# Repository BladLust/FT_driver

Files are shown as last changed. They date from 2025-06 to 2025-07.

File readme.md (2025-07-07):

## 硬件准备及安装

由于使用的FT电机与Leap Hand原装XC330电机尺寸、转轴、固定孔位置**完全相同**，仅有控制线插口位置不同，我们可以大致使用教程https://v1.leaphand.com/assembly

进行灵巧手硬件的安装。但正由于其控制线插口位置不同，我们需要对部分XC330配套的结构件进行调整并以3D打印的方式制作，我们需要替换其中由Dynamixel提供的电机支撑件。具体地，将所需的11个H101，10个S101以及6个S102使用本项目中`STLSubstitute`文件夹中对应的模型替换（由于它们足够相似，仿真中可以不用替换）。其中S101有两个版本，分别是需要8片的普通版和2片的Slim版。Slim版用于侧面不能突出的大拇指第二关节部分。

#### 3D打印部分

从LeapHand官网下载对应的模型进行打印，与本项目中提供的结构件一起即可组成灵巧手的全部硬件结构。官网下载部分的模型对于精度及强度要求均略低于直接用于固定电机的结构件，经过我们测试全部使用PLA进行打印即可满足基本强度要求，但使用更加坚固的PETG进行打印有助于减少需要由于误操作部件损坏重新组装灵巧手的次数。

#### 硅胶指尖制作

我们的演示程序使用的并非原版的Leap Hand灵巧手指尖。这些特制的指尖由硅胶倒模方式制作，经测试5度硅胶效果最好。在`CustomTip`文件夹中有制作硅胶部分用的内外模具的模型（取决于计划一次做好或分四次完成，打印4份或1份）及为指尖提供结构强度的”指骨“模型（安装在每个手指上，需要4个）。具体制作过程如下

- 打印内外模具（内模需要打印支撑以免打印失败）
- 在将与硅胶接触的部分涂抹一薄层凡士林以便之后脱模
- 在外模内倒入硅胶，以插入内模后刚好液面可接触到内模顶盖处为佳
- 放置与冰箱冷藏室中减速凝固，以便气泡排出。
- 在执行下一步之前先按照Leap Hand官方教程为指骨埋入土字铜花母
- 待其凝固后（具体多久并未测试，但放一晚肯定够了）脱模，并使用束带将其固定在指骨上。

#### 电机初始设置

12V DC电源上电，使用本项目中附带，由飞特提供的上位机软件`FD.exe` 进行各电机ID设置与波特率设置。（除非你懂得如何修改相关文件，不然推荐使用我们的电机ID顺序，如下图，波特率同理）。除大拇指外的三只手指从手掌到指尖按结构顺序ID分别为[x+1, x, x+2, x+3]，手指顺序为食指、中指、四指、拇指。对全新电机进行设置的具体顺序如下：

- 连接**单一一个电机**打开上位机软件，左上方波特率选择1000000，打开接口并电机搜索。
- 理论上新电机会以ID=1的状态被搜到，点击左侧搜到的电机，选择中上方的Programming页面。这里是各个寄存器的值，你可以通过这个界面具体检查电机各项设置
- 将ID改为你所需要的ID（我们建议先将16个电机依次更改ID为0-15并贴条记录，之后安装时按照对应ID安装）。**如果你不知道你在做什么，请保持副ID（Secondary ID)与主ID相同**
- 更改后电机会成为断连状态，重新给电机上电后重新搜索，电机将以新的ID出现。回到Programming界面将波特率baudrate改为115200。
- 换一个电机，重复以上步骤直至全部16个电机完成初始ID设置。

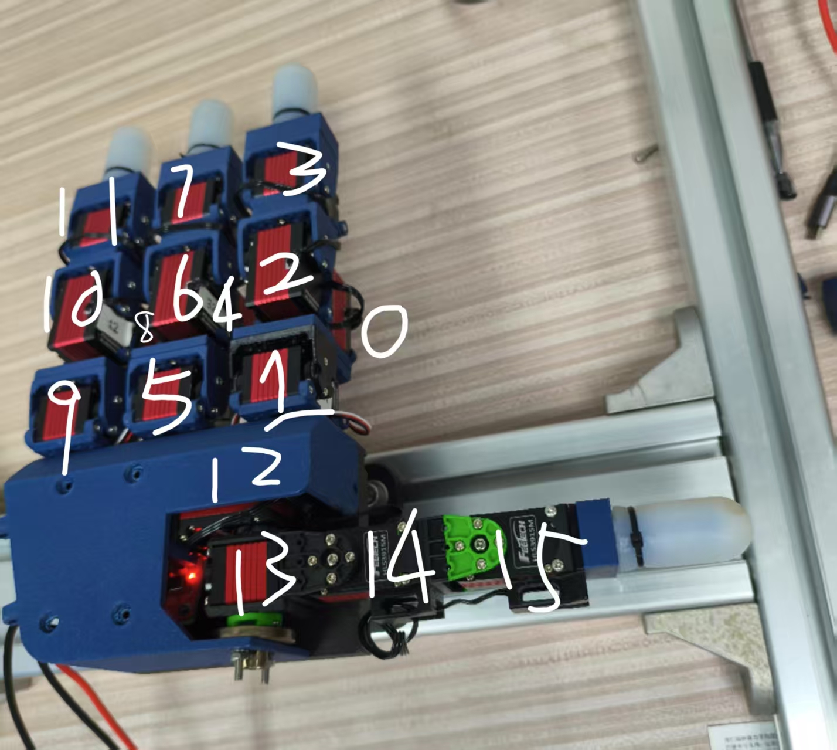
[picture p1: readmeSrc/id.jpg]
id


#### 组装

基本组装流程和LeapHand完全相同，但有几点需要注意

- 由于我们更改了S101及H101的模型，现在H101不同于原版，由于其单侧开槽的原因具有方向性。这一特点是为了能让螺丝固定部分更宽的修改版S101不影响手指活动空间的设计。你可以通过在一个单独电机上同时安装S101和H101了解其结构关系。在组装时应注意H101的开槽要面向S101一侧，具体地，对于2、3、4指来说其每指三个H101开槽的方向以手掌到指尖的顺序依次为掌心、手背、掌心。
- 电机有安装方向之分，但不管装正装反都不影响灵巧手本质结构，可以用电机Logo及型号两面的朝向分辨其安装方向。我们组装的灵巧手各电机方向如下图（2、3、4指朝向相同），如果你组装的手和我们的电机朝向相同，那么在完成后续“电机设置”一节完成后你应该得到正方向与Leap Hand官方仿真完全相同的结果。你可以选择使用与我们相反的方向安装0,3,4,7,8,11,12,13号电机，即可在后续“电机设置”一节中跳过使用mode3将电机反向的步骤。
- 组装过程中请时刻注意舵机间3pin接线的正反，若接反有烧毁舵机的风险！！！

| 拇指 | 其余三指 |
| :---: | :---: |
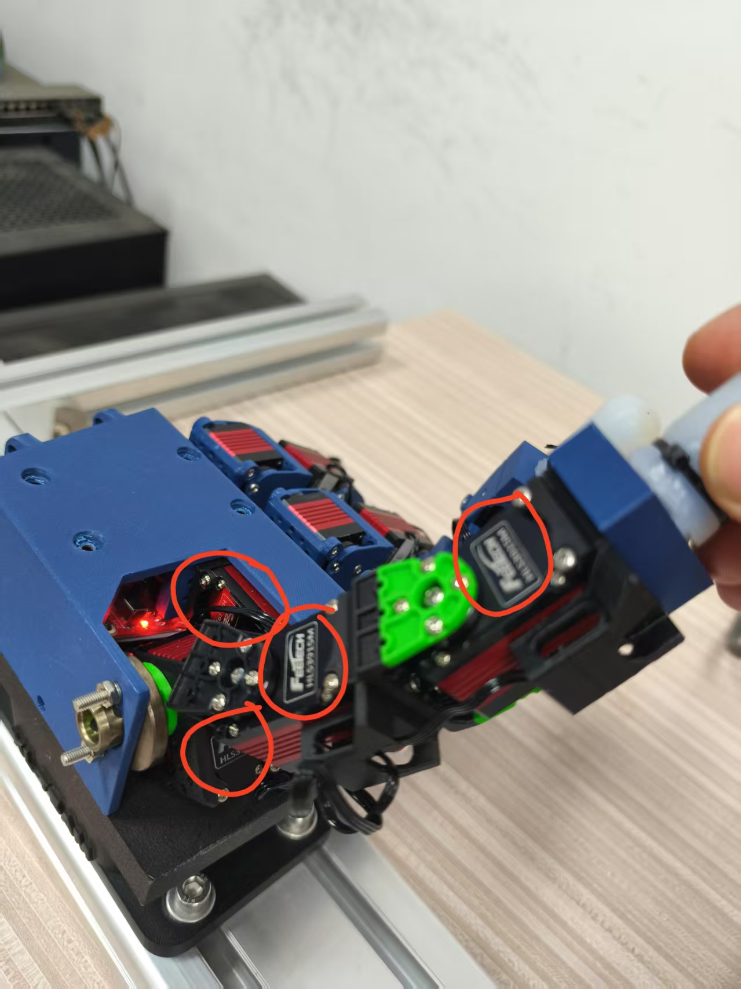
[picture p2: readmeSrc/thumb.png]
thumb
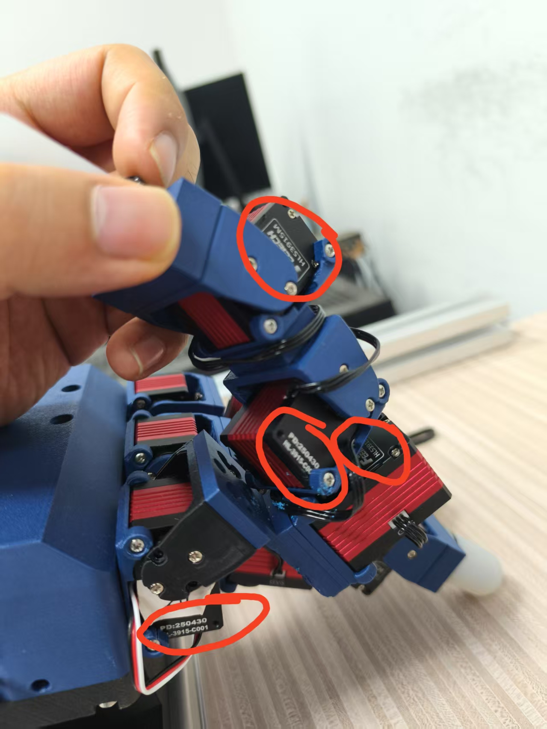
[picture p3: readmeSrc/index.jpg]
index
|  |  |

## 安装飞特电机驱动&调试电机

####  环境安装与初次运行

**注意：在进行这一步之前你需要先决定使用ROS2或ROS1,因为其涉及的python版本不同。而由于ROS对于虚拟环境的支持问题，我们需要将后续所有会在硬件侧ROS node中用到的包都装在对应版本的系统python中。当然如果你不确定，你可以可以先在任意一个版本的python下安装调试
**注意：ROS1中使用的是python3.8
**。*以下以ROS2使用的Python3.10为例*  

```shell
sudo apt install python3-pip #万一有人还没装pip
python3.10 -m pip install ftservo-python-sdk numpy # 飞特电机官方SDK & numpy
sudo apt-get purge brltty # 卸载BrailleTTY盲人输入装置驱动，这东西会很霸道地hijack每个插入的serial设备，除非你会使用这种装置，建议直接卸载。如果你遇到插上手搜不到/dev/ttyUSB0,很可能是它的问题。
sudo usermod -a -G dialout $USER #我们的灵巧手是用Serial方式连接在电脑上的，对于Linux来说，它需要dialout权限才能存取这种设备，这里是赋予本用户这个权限
```

由于我们更改了本用户权限，重启电脑才能使这个改动发挥作用（log out都不行）。之后使用对应版本的python运行`FT_Client.py`，这是主要的硬件控制api，但直接运行它可以帮助你进行调试。调试程序有两个版本：mode 0 只读取每个关节目前的角度而不进行控制，而mode 1 则让每个关节进行小幅正弦波摆动。目前我们**还未对电机进行归零，使用mode1有炸机风险**。运行mode 0：

```SHELL
python3.10 ./scripts/FT_client.py -m 0,1,2,3,4,5,6,7,8,9,10,11,12,13,14,15 --mode 0 #-m指定电机ID,尽量别动。其它设置还有 --units {deg, rad}可以选择使用角度或弧度作为单位等，具体可以不带参数跑一遍这个脚本查看提示，或直接查看源码
```

观察到以下格式输出即为成功，此时手动移动各关节可以看到对应手指关节角变动。这也将是之后检查归零和电机正方向设置情况的主要方式。其顺序为ID从0至15每4个一行，其中每一行为一根手指，顺序为食指、中指、四指、拇指。行内电机顺序大体上为从掌心到指尖的连接顺序，但对于2、3、4指来说略有不同。以二指为例，其关节ID按从掌心到指尖的连接顺序其实为[1,0,2,3]，这与原Leap Hand的顺序设计相同。

```
--- Feetech Motor Monitor (Mode 0) | Units: deg ---
Timestamp: 2025-06-29 17:21:02

--- Randomly Sampled PID Gains (P, D, I) ---
  Showing Motor ID 13: P=30  D=70  I=0  
Read Position:
183.36	156.21	155.77	172.99
182.05	157.79	149.17	231.18
194.26	155.85	153.22	275.30
147.68	260.71	183.45	182.22

--- Motor State (deg, deg/s) ---

```

#### 电机设置

在这一节中我们将使用`FT_setting_editor.py`进行电机初始状态的设定。此脚本有较为良好的界面，本质上按照界面提示操作即可，此处列出全新电机在**硬件安装与本教程相同的情况下**应进行的调整列表：

- 使用mode1对所有电机的默认PID进行更改，P=30, D=70, I=0。电机重新上电后启效。
- 使用mode3确认18号寄存器1byte长度初值。应均为116。
- 使用mode2将0,3,4,7,8,11,12,13号电机的18号寄存器写入1byte长数据值226。可以看到这是在116的基础上翻转了3个bit的结果，此设置可以使对应电机反向。如果你的电机初值与我不同，在型号相同的情况下翻转此3bit亦可完成反向。
- **我们强烈建议你参照Leap Hand各电机的正方向（向该方向旋转角度增加）检查一遍**：对于大拇指来说，正方向由手掌至指尖为：掌心、逆时针、掌心、掌心。其余三指由手掌至指尖：掌心、左、掌心、掌心。
- 使用mode0依次将所有电机的中点归零到起始位置，其中起始位置如下图所示（特别注意大拇指旋转电机的起始位置，以捋线槽为基准。

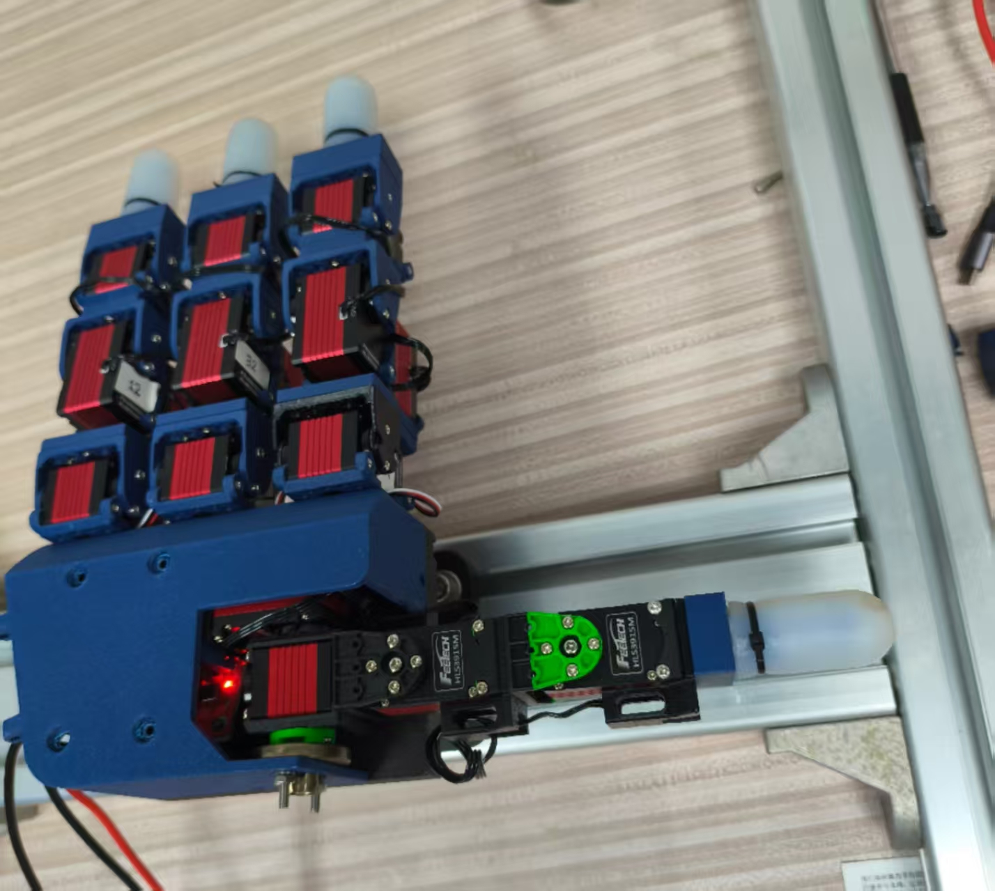
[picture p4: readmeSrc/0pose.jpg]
0pose


## 手内方块翻转项目移植与运行  

####  环境安装

**注意：为方便移植，本项目ROS1中使用的是python3.8
- 参考原项目的教程 https://github.com/RGMC-XL-team/inhand_reorientation 
- 请严格安装除了Dynamixel SDK以外的所有软件和依赖项
- 新建workspace，在src中克隆两个项目的源码：https://github.com/RGMC-XL-team/inhand_reorientation    https://github.com/Rice-RobotPI-Lab/RGMC_In-Hand_Manipulation_2024
- 在~leap_hardware/src/leap_hardware路径下添加文件（夹）scservo_sdk、sms_sts、FT_client.py
- 在~leap_hardware/scripts下将原leaphand_node.py替换为我们提供的leapnode_FT.py
- 同时修改~leap_hardware下的CMakeLists.txt，按上一步骤修改leapnode节点文件名，确保编译通过
```shell
cd path-to-your-workspace/
catkin_make_isolated
```

####  参数调整和整体准备

**注意：该步骤需要我们熟悉项目结构，对参数文件和launch文件进行修改

- 在~leap_hardware/launch/下修改system.launch文件，参数设置除"free_move"外均为true；设置同路径single_camera.launch中参数“camera_0_serial_no“为你的相机序列号
- 将灵巧手固定在机架（由铝材搭接而成）上，操作平面打印件可以用魔术贴贴在掌心，确保凹槽对齐，固定相机于手掌正上方约40cm处，确保相机垂直投影于操作平面
- 打印方块（已提供cube_s.stl文件），按照教程：https://github.com/Rice-RobotPI-Lab/RGMC_In-Hand_Manipulation_2024
          按要求打印二维码并粘贴到方块中,可供参考的二维码下载地址：https://chev.me/arucogen/
- 请自行进行相机标定，然后将标定结果写入~leap_hardware/config/rgmc_d405_calib.yaml中
- 方块A面朝上，置于操作平面正中心
- 保证舵机通信、控制正常，接线合理，供电达标

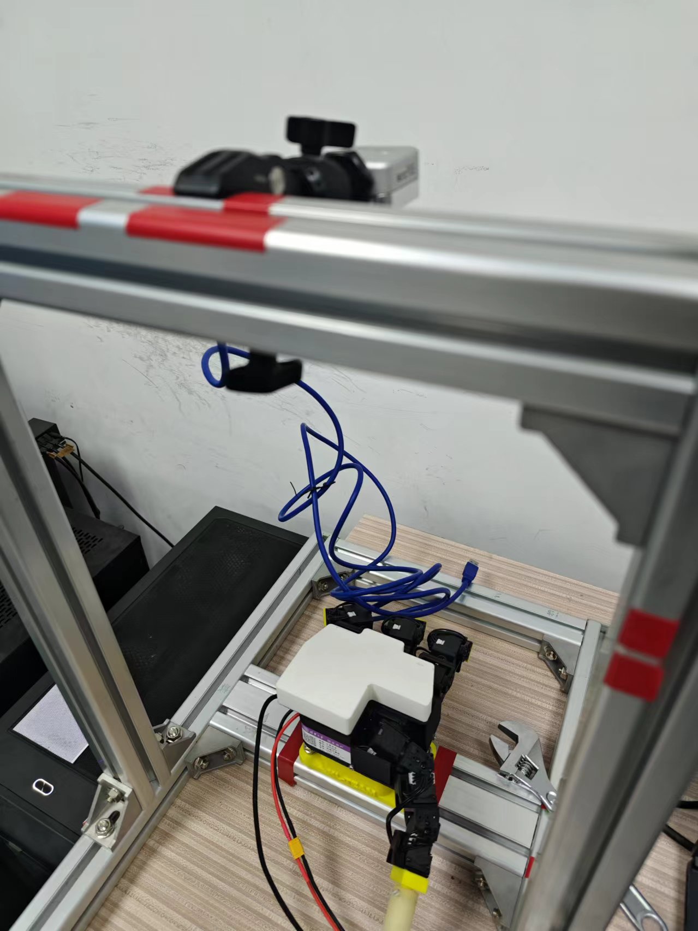
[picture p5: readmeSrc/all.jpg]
all


####  运行程序

第一个终端进行通讯，展示可视化界面
```shell
conda deactivate 
cd path-to-your-workspace/
source devel_isolated/setup.bash
roslaunch leap_hardware system.launch 
```
此时灵巧手将调整为初状态，rviz界面中若观察到cube坐标系x-y轴、操作平面凹陷处、掌心缺口处“三处虎口对齐”，cube坐标系的零点在Z方向略高于操作平面，则相机标定结果合理；若误差较大可适当调整~leap_hardware/config/rgmc_d405_calib.yaml中相机参数。

第二个终端跑RL模型
```shell
conda activate rlgpu
cd ~leap_sim/leapsim/hardware
python ./agent_hw.py
```
若提示：Software is initialized successfully!   Hardware is initialized successfully! 则说明模型载入完成

第三个终端跑上位机决策
```shell
conda activate rlgpu
cd ~leap_task_B/scripts
python ./taskB_highlevel.py
```
运行后，开始跑taskB，即按照ABCDEFEDCBA的循环顺序将手内方块连续翻转十几轮后停止

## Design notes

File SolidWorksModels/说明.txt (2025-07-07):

此处为飞特舵机版leap hand的sw模型文件，但还没有更新STLSubstitute中的加强版模型

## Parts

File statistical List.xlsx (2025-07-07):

 | 序号 | 类型 | 型号/名称 | 数量 | 来源/工艺 | 备注
灵巧手部分 | 1 | 飞特舵机 | HLS3915M-C001 | 16 | 采购
 | 2 | 飞特调试板 | URT-1 | 1 | 采购
 | 3 | uni-trend电源 | UTP1306S | 1 | 采购 | 可换用其他12V 6A供电DC电源
 | 4 | 指尖 | Fingertip | 4 | 3D打印 | 非标
 | 5 | 指尖硅胶套 |  | 4 | 硅胶注塑 | 非标，可提供模具文件
 | 6 | U型件 | H101 | 11 | 3D打印 | 非标
 | 7 | 长侧面连接件 | S101 | 10 | 3D打印 | 非标
 | 8 | 短侧面连接件 | S102 | 6 | 3D打印 | 非标
 | 9 | 导线件 | Cable Spacer | 5 | 3D打印 | 非标
 | 10 | MCP板件 | MCP Bracket | 3 | 3D打印 | 非标
 | 11 | 垫块 | DIP Spacer | 3 | 3D打印 | 非标
 | 12 | 手掌 | Palm Lower | 1 | 3D打印 | 非标
 | 13 | 手掌背板 | Palm Upper | 1 | 3D打印 | 非标
机架部分 | 14 | 底座 | hand_mount (https://github.com/BladLust/FT_driver/blob/main/hand_mount.3mf) | 1 | 3D打印 | 非标
 | 15 | 铝型材4040 长400mm |  | 1 | 采购
 | 16 | 铝型材4080 长400mm |  | 1 | 采购
 | 17 | 铝型材4040 长600mm |  | 4 | 采购
 | 18 | 铝型材4040角码连接件 |  | 10 | 采购
 | 19 | realsense相机 | D405 | 1 | 采购
 | 20 | Ulanzi相机夹具 | R099 | 1 | 采购
操作对象 | 21 | 方块 |  | 1 | 3D打印 | 非标，方块模型和二维码地址：https://github.com/Rice-RobotPI-Lab/RGMC_In-Hand_Manipulation_2024
 | 22 | 操作平面 |  | 1 | 3D打印 | 非标
标准件 | 23 | M3 6mm Screws (https://a.co/d/fi2Dbrr) |  | 5 | 采购
 | 24 | M2 6mm Screws (https://a.co/d/5StKiN7) |  | 4 | 采购
 | 25 | M2 10mm Screws (https://a.co/d/5StKiN7) |  | 24 | 采购
 | 26 | M2 8mm Screws (https://a.co/d/5StKiN7) |  | 16 | 采购
 | 27 | M2 6mm 3D printer Inserts (https://a.co/d/eFoiS2e) |  | 24 | 采购
 | 28 | M3 6mm 3D printer Inserts (https://a.co/d/eFoiS2e) |  | 5 | 采购
 | 29 | 十字槽沉头螺钉 | M6×50 | 4 | 采购
连线 | 30 | 相机数据线 | USB转Micro-B | 1 | 采购
 | 31 | 香蕉头转XT30线 |  | 1 | 采购
 | 32 | XT30公母线 | XT30 Pigtail | ≥2 | 采购
 | 33 | XT30转五路线 |  | 1 | 焊接 | 非标，用舵机线和XT330公母线进行焊接
部分参考：https://v1.leaphand.com/parts

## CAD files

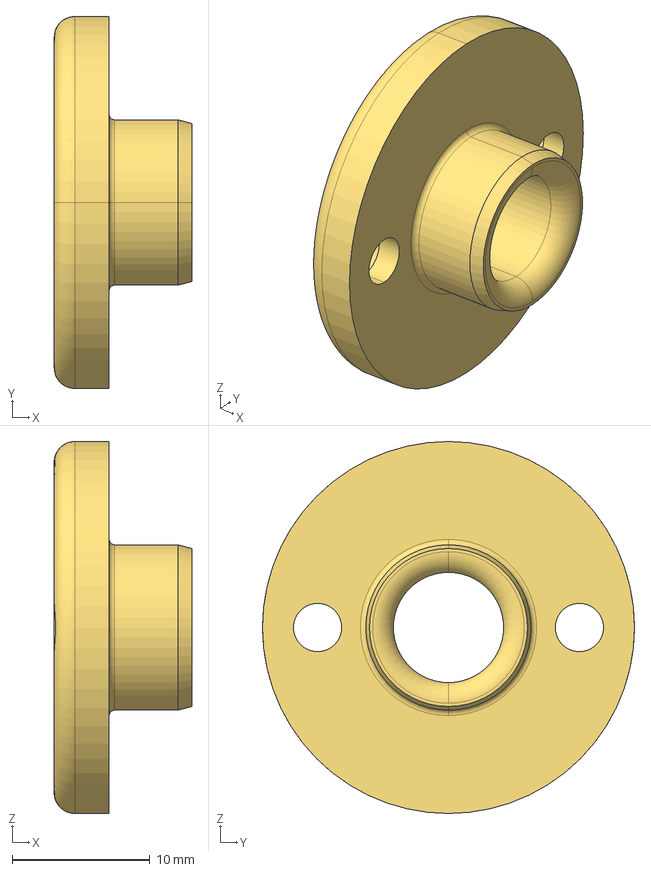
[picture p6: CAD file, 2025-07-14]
SolidWorksModels/BWYI-C-d8-L10.step
10.0 x 27.0 x 27.0 mm

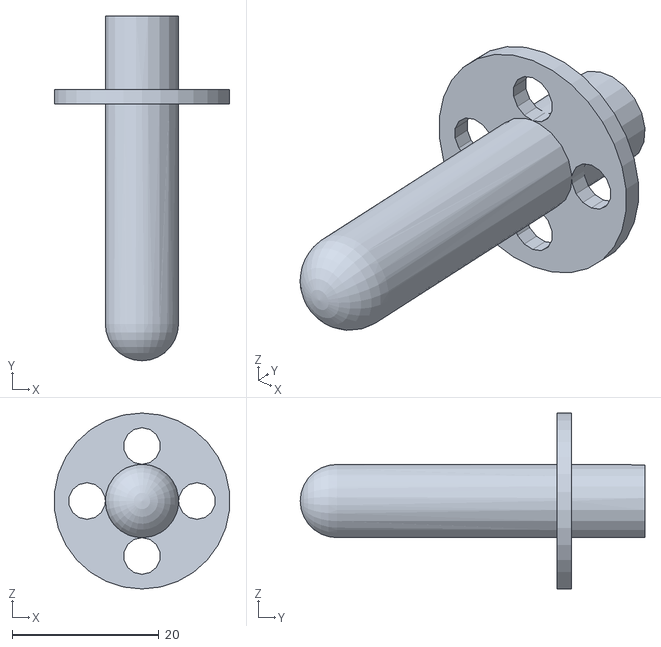
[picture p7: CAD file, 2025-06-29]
STL/CustomTip/硅胶模具_内.STL
23.9 x 47.0 x 24.0

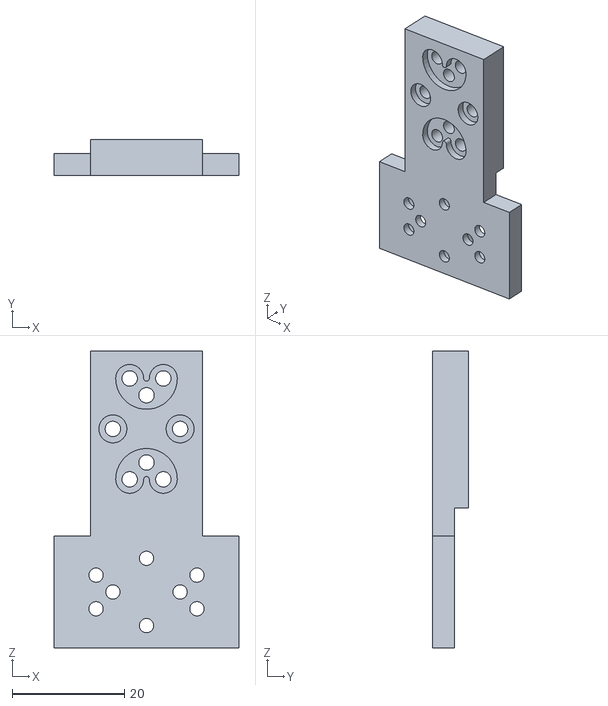
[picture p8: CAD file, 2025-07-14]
STL/mcp_bracket.STL
33.0 x 6.50 x 53.0

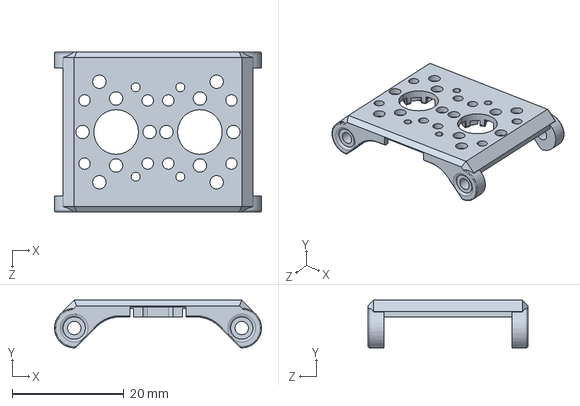
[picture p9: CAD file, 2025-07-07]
SolidWorksModels/S101_Slim.sldprt
37.1 x 8.54 x 28.6 mm

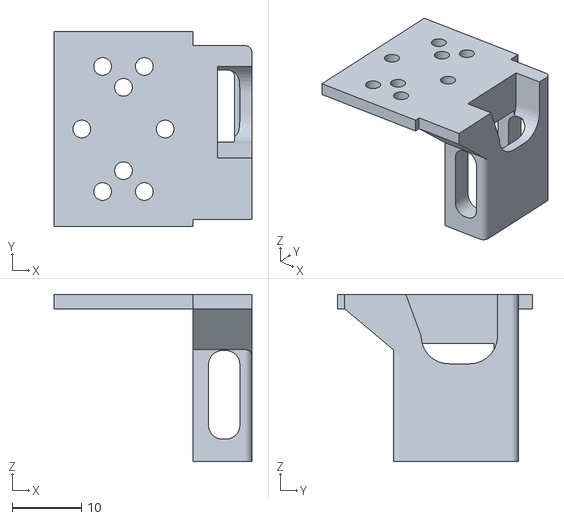
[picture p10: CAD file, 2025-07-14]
STL/cable_spacer.STL
28.5 x 28.0 x 24.1

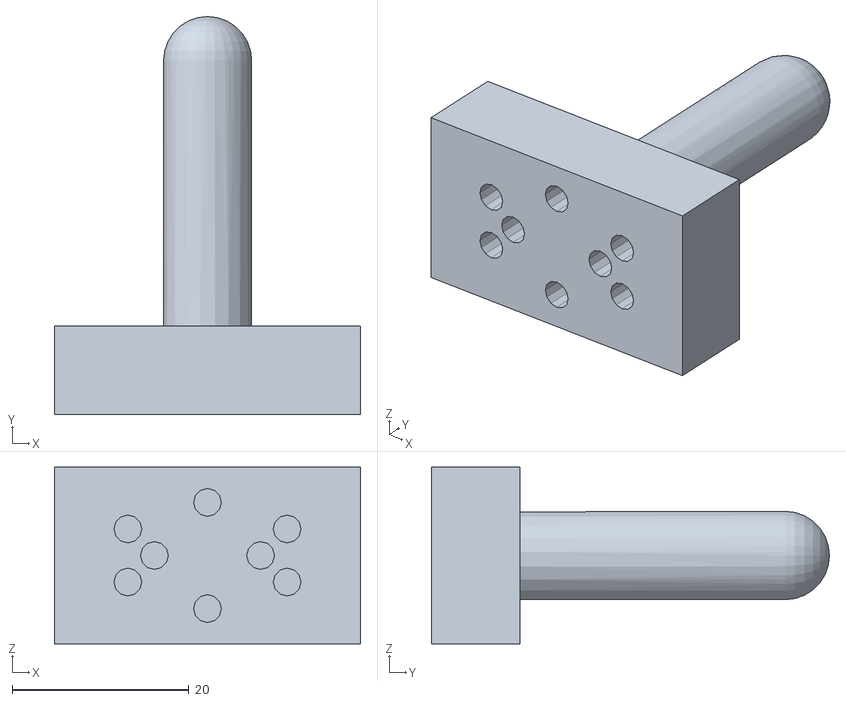
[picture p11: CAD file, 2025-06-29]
STL/CustomTip/fingertip_custom_real.STL
34.6 x 45.0 x 20.0

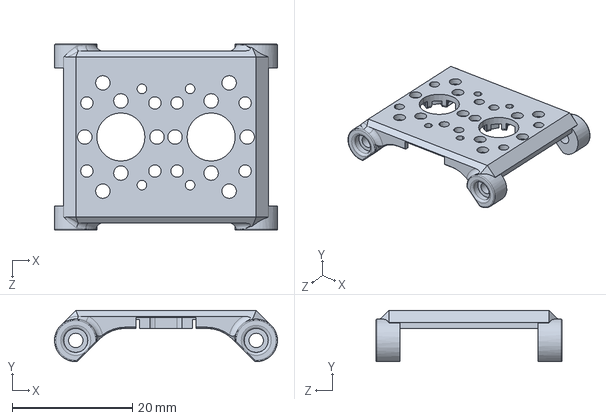
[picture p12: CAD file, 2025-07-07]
SolidWorksModels/S101.sldprt
37.1 x 8.54 x 31.0 mm

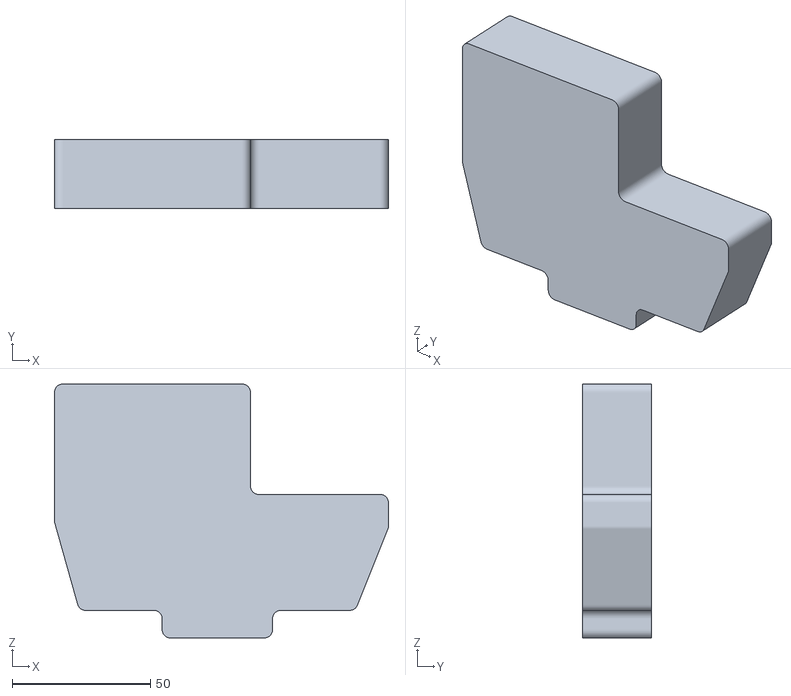
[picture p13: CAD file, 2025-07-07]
STL/control_platform.STL
121.0 x 25.0 x 92.0

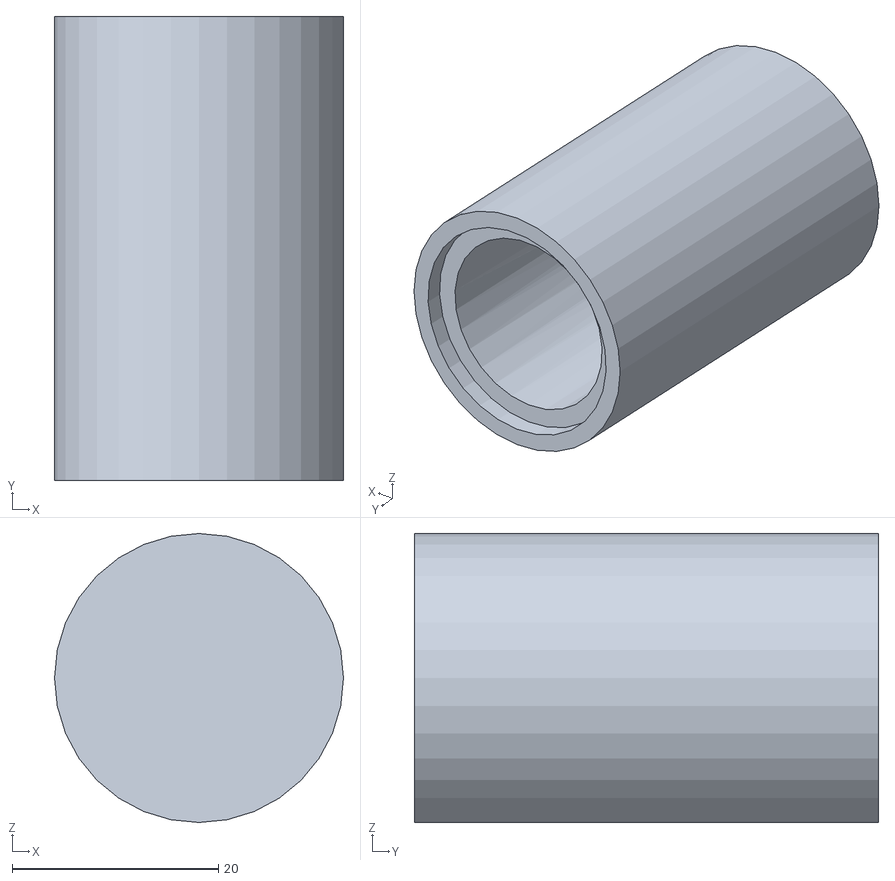
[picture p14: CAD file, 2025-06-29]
STL/CustomTip/硅胶模具_外.STL
28.0 x 45.0 x 28.0

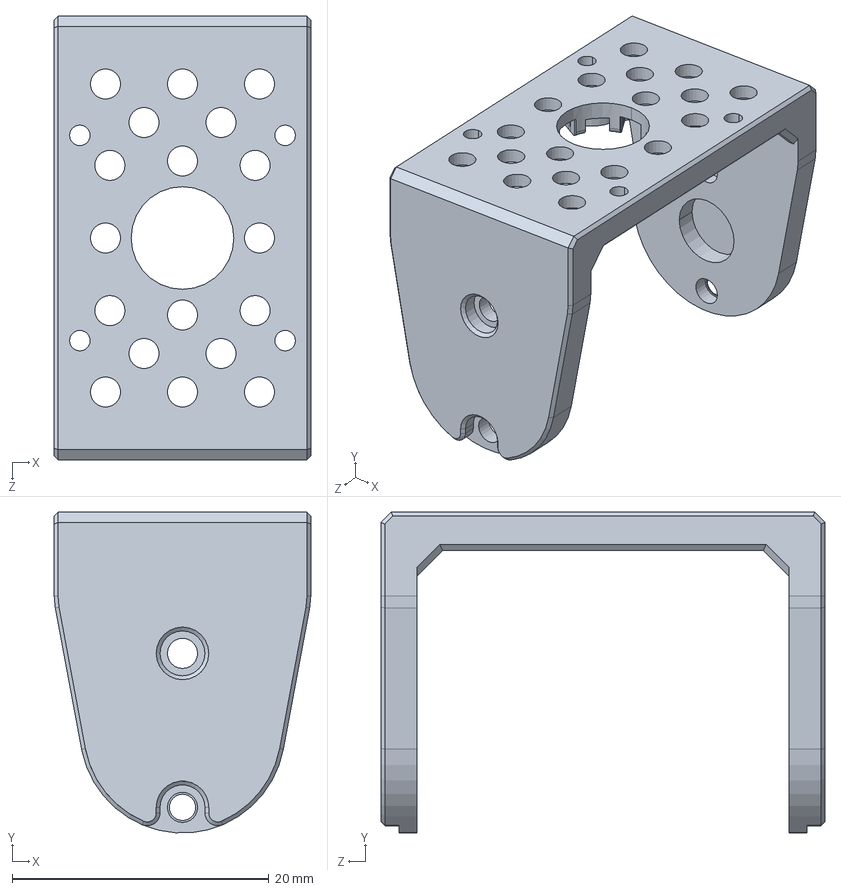
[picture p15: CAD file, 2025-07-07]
SolidWorksModels/H101.SLDPRT
20.0 x 25.0 x 34.6 mm

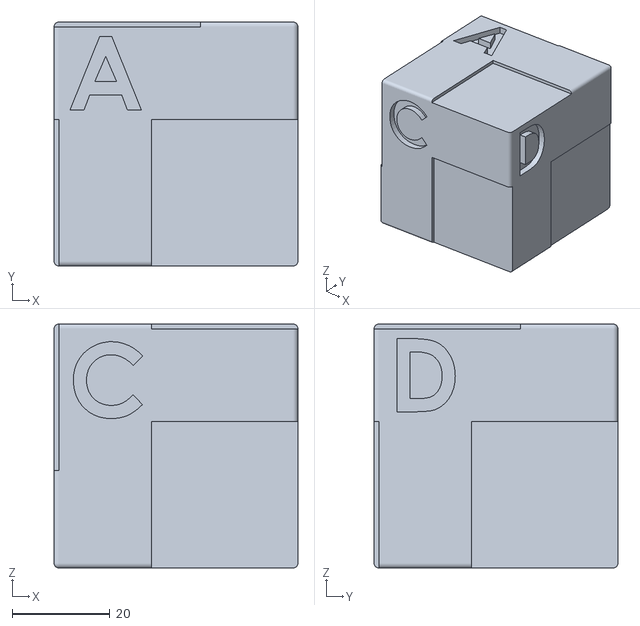
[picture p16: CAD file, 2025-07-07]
STL/cube_s.STL
50.0 x 50.0 x 50.0

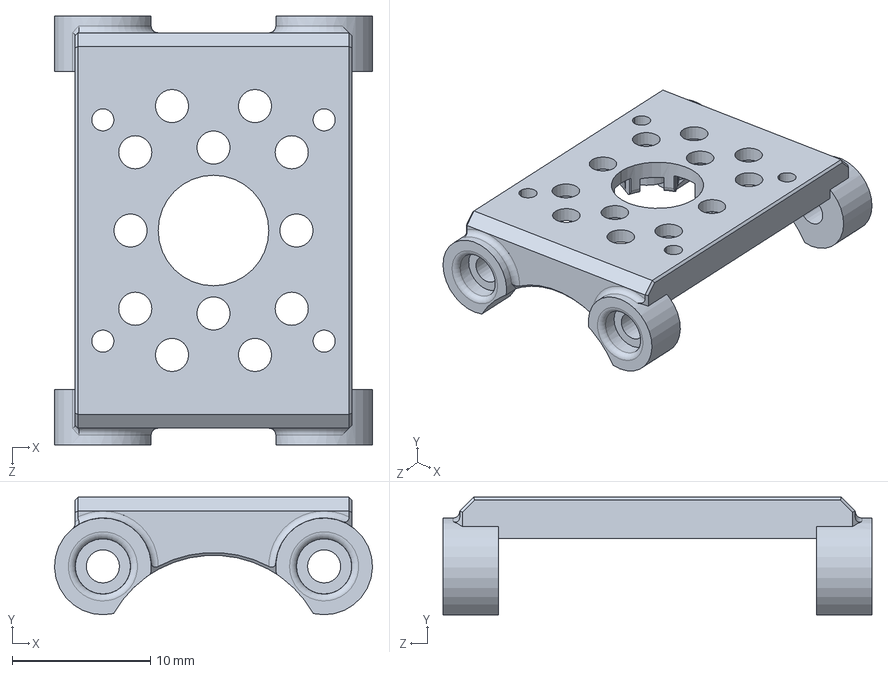
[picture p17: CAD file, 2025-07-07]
SolidWorksModels/S102.sldprt
23.0 x 8.50 x 31.0 mm

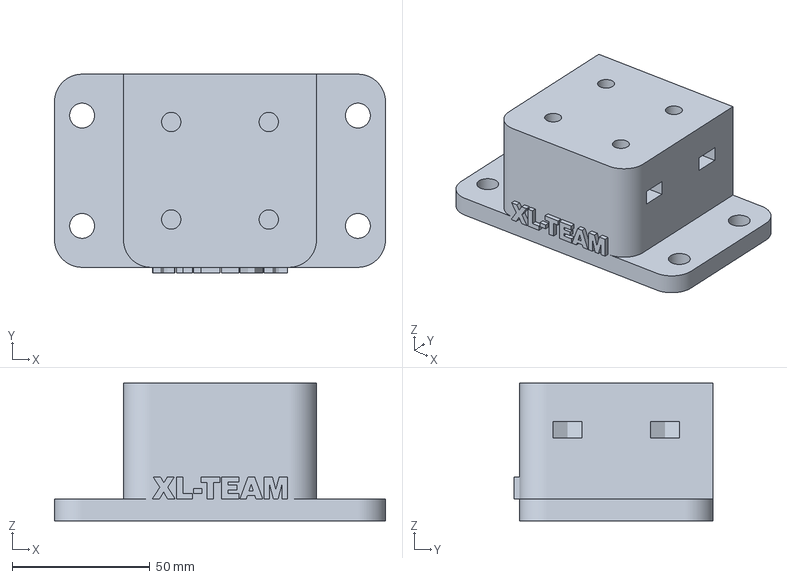
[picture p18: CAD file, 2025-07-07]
STL/hand_mount.3mf
120.0 x 72.0 x 50.0 mm

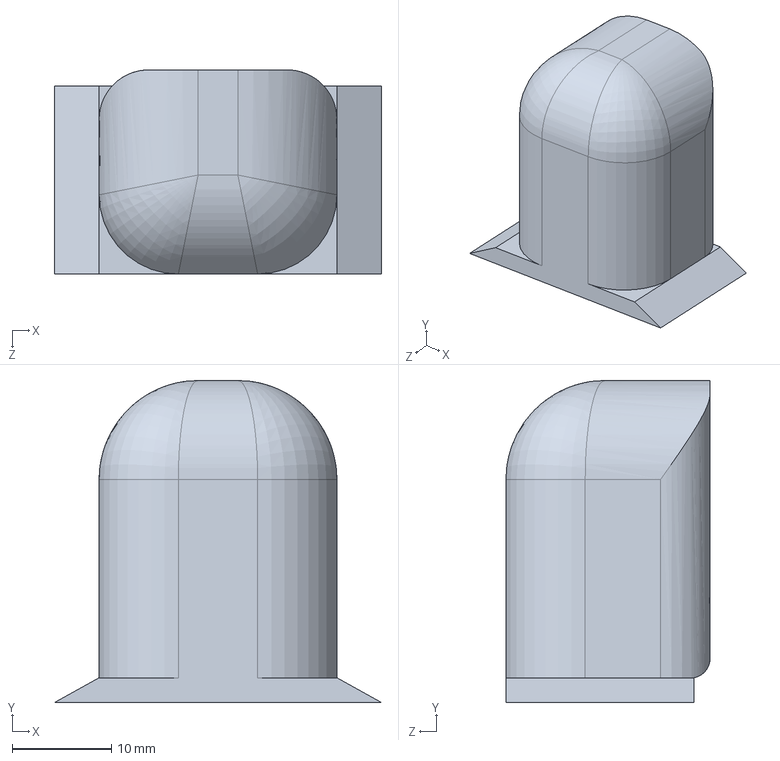
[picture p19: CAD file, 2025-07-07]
SolidWorksModels/finger_tip_simple.SLDPRT
33.0 x 32.5 x 20.6 mm

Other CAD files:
SolidWorksModels/FT-Hand3-Thumb.SLDASM
SolidWorksModels/FT-Hand3.SLDASM
SolidWorksModels/操作平面.SLDPRT
SolidWorksModels/U形板.SLDPRT
STL/H101.STL
STL/S101.STL
STL/S101_Slim.STL
STL/S102.STL
STL/dip_spacer.STL
SolidWorksModels/FT短连接件_加固.SLDPRT
SolidWorksModels/FT长连接件_加固.SLDPRT
SolidWorksModels/URT.SLDPRT
SolidWorksModels/U形板-开槽.SLDPRT
SolidWorksModels/cable_spacer2.SLDPRT
SolidWorksModels/dip_spacer.SLDPRT
SolidWorksModels/lower_palm_3.SLDPRT
SolidWorksModels/mcp_bracket_3.SLDPRT
SolidWorksModels/圆柱垫块.SLDPRT
SolidWorksModels/轴顶2.SLDPRT

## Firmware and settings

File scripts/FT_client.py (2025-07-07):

#!/usr/bin/env python

# This is based off of the Feite SDk
from scservo_sdk import *
import atexit
import logging
import os
import time
import random
from typing import Optional, Sequence, Tuple, Union

import numpy as np

# --- Control Table Addresses ---
# Using the address definitions from the official SDK is more reliable.
SMS_STS_TORQUE_ENABLE = 40
SMS_STS_ACC = 41
SMS_STS_GOAL_POSITION_L = 42
SMS_STS_GOAL_SPEED_L = 46

# PID Gain Addresses for Position Loop
SMS_STS_KP1_L = 50
SMS_STS_KD1_L = 51
SMS_STS_KI1_L = 52

SMS_STS_PRESENT_POSITION_L = 56
SMS_STS_PRESENT_SPEED_L = 58
SMS_STS_PRESENT_CURRENT_L = 69
SMS_STS_PRESENT_VOLTAGE = 62

# --- Data Byte Lengths ---
LEN_PRESENT_POSITION = 2
LEN_PRESENT_SPEED = 2
LEN_PRESENT_CURRENT = 2
LEN_PRESENT_VOLTAGE = 1

# --- Unit Conversions ---
# 4096 ticks per revolution -> radians
DEFAULT_POS_SCALE_RAD = 2.0 * np.pi / 4096
DEFAULT_VEL_SCALE_RAD = 0.732 * 2.0 * np.pi / 60.0  # 0.732 rpm per unit -> rad/s
DEFAULT_POS_SCALE_DEG = 360.0 / 4096  # 4096 ticks per revolution -> degrees
DEFAULT_VEL_SCALE_DEG = 0.732 * 360.0 / 60.0  # 0.732 rpm per unit -> deg/s
DEFAULT_CUR_SCALE = 6.5 / 1000.0  # 6.5mA per unit -> Amperes
DEFAULT_VLT_SCALE = 0.1  # 0.1V per unit -> Volts


def signed_to_unsigned(value: int, size: int) -> int:
    """
    Converts a signed integer to its sign-magnitude representation for
    writing to the servo.
    """
    bit_size = 8 * size
    sign_bit_mask = 1 << (bit_size - 1)

    if value < 0:
        # Get magnitude and set the sign bit
        magnitude = abs(value)
        return sign_bit_mask | magnitude
    else:
        # Positive value is its own representation
        return value


def unsigned_to_signed(value: int, size: int) -> int:
    """
    Converts a value from its sign-magnitude representation as read from
    the servo.
    """
    bit_size = 8 * size
    sign_bit_mask = 1 << (bit_size - 1)
    magnitude_mask = sign_bit_mask - 1

    # Check if the sign bit is set
    if (value & sign_bit_mask) != 0:
        # It's a negative number. Get the magnitude from the remaining bits
        # and return it with a negative sign.
        magnitude = value & magnitude_mask
        return -magnitude
    else:
        # It's a positive number. The value is its own magnitude.
        return value


class FTClient:
    # --- Class-level tracking of open clients for cleanup ---
    OPEN_CLIENTS = set()

    def __init__(
        self,
        motor_ids: Sequence[int],
        port: str = "/dev/ttyUSB0",
        baudrate: int = 115200,
        use_degrees: bool = True,
    ):
        self.motor_ids = list(motor_ids)
        self.port_name = port
        self.baudrate = baudrate
        self._is_connected = False
        self.use_degrees = use_degrees

        self.port_handler = PortHandler(self.port_name)
        self.packet_handler = sms_sts(self.port_handler)

        if self.use_degrees:
            self.pos_scale = DEFAULT_POS_SCALE_DEG
            self.vel_scale = DEFAULT_VEL_SCALE_DEG
        else:
            self.pos_scale = DEFAULT_POS_SCALE_RAD
            self.vel_scale = DEFAULT_VEL_SCALE_RAD

        self.cur_scale = DEFAULT_CUR_SCALE

        # Initialize the new, efficient readers
        self._pos_vel_reader = FTPosVelReader(self, self.motor_ids)
        self._pos_reader = FTPosReader(self, self.motor_ids)
        self._vel_reader = FTVelReader(self, self.motor_ids)

    @property
    def is_connected(self) -> bool:
        """Returns the connection status of the client."""
        return self._is_connected

    def connect(self):
        """Connects to the FT motors. Does NOT enable torque by default."""
        if self._is_connected:
            logging.warning("Client is already connected.")
            return

        if not self.port_handler.openPort():
            raise OSError(f"Failed to open port: {self.port_name}")
        logging.info("Succeeded to open port: %s", self.port_name)

        if not self.port_handler.setBaudRate(self.baudrate):
            raise OSError(f"Failed to set baudrate to {self.baudrate}")
        logging.info("Succeeded to set baudrate to %d", self.baudrate)

        self._is_connected = True
        FTClient.OPEN_CLIENTS.add(self)

    def disconnect(self):
        """Disconnects from the ft device. Assumes torque has been handled."""
        if not self._is_connected:
            return
        self.port_handler.closePort()
        self._is_connected = False
        if self in FTClient.OPEN_CLIENTS:
            FTClient.OPEN_CLIENTS.remove(self)

    def set_torque_enabled(self, motor_ids: Sequence[int], enabled: bool):
        """Enables or disables torque for the specified motors."""
        self.check_connected()
        for motor_id in motor_ids:
            comm_result, ft_error = self.packet_handler.write1ByteTxRx(
                motor_id, SMS_STS_TORQUE_ENABLE, int(enabled)
            )
            self.handle_packet_result(
                comm_result, ft_error, motor_id, context=f"set_torque_enabled={enabled}"
            )

    def read_pid_gains(self) -> dict:
        """Reads the PID gains from all motors individually."""
        self.check_connected()
        pid_gains = {}
        logging.info("Reading PID gains from all motors...")
        for motor_id in self.motor_ids:
            # readTxRx reads a block of a given length. Here we read 3 bytes starting from the P-gain address.
            data, comm_result, error = self.packet_handler.readTxRx(
                motor_id, SMS_STS_KP1_L, 3
            )
            if self.handle_packet_result(
                comm_result, error, motor_id, "read_pid_gains"
            ):
                if data and len(data) == 3:
                    # Order from spec is P (50), D (51), I (52)
                    p, d, i = data
                    pid_gains[motor_id] = {"P": p, "D": d, "I": i}
                else:
                    logging.error(
                        f"[ID:{motor_id:03d}] Failed to get valid PID data packet."
                    )
                    pid_gains[motor_id] = {"P": -1, "D": -1, "I": -1}  # Indicate error
            else:
                pid_gains[motor_id] = {"P": -1, "D": -1, "I": -1}
        return pid_gains

    def set_pid_gains(self, p: int, i: int, d: int):
        """
        Sets the Position, Integral, and Derivative gains for the position loop
        for all motors using a single synchronous write command.
        """
        self.check_connected()
        logging.info(f"Setting PID gains for all motors to: P={p}, I={i}, D={d}")

        pid_sync_writer = GroupSyncWrite(self.packet_handler, SMS_STS_KP1_L, 3)
        # Note the order for the write packet is P, D, I
        param_pid = [p, d, i]

        for motor_id in self.motor_ids:
            addparam_result = pid_sync_writer.addParam(motor_id, param_pid)
            if not addparam_result:
                logging.error(
                    f"[ID:{motor_id:03d}] Failed to add PID gains to sync write packet."
                )

        comm_result = pid_sync_writer.txPacket()
        self.handle_packet_result(comm_result, context="set_pid_gains")
        pid_sync_writer.clearParam()

    def read_pos_vel(self) -> Tuple[np.ndarray, np.ndarray]:
        """Returns the current positions and velocities from all motors."""
        return self._pos_vel_reader.read()

    def read_pos(self) -> np.ndarray:
        """Returns the current positions from all motors."""
        return self._pos_reader.read()

    def read_vel(self) -> np.ndarray:
        """Returns the current velocities from all motors."""
        return self._vel_reader.read()

    def HLSSyncWritePosEx(self, motor_id, position, vel, acc):
        txpacket = [
            acc,
            self.packet_handler.scs_lobyte(position),
            self.packet_handler.scs_hibyte(position),
            self.packet_handler.scs_lobyte(1500),
            self.packet_handler.scs_hibyte(1500),
            self.packet_handler.scs_lobyte(vel),
            self.packet_handler.scs_hibyte(vel),
        ]
        print(f"HLSSyncWritePosEx: ID={motor_id}, Pos={position}, Vel={vel}, Acc={acc}")
        return self.packet_handler.groupSyncWrite.addParam(motor_id, txpacket)

    def write_desired_pos_simple(self, motor_ids: Sequence[int], positions: np.ndarray):
        """
        Writes desired positions with fixed velocity (1000) and acceleration (0).
        This is a simplified method for basic position control.
        """

        pos_now = positions-3.14
        print("Command Position:")
        for i in range(0, len(pos_now), 4):
            print(
                f"{pos_now[i]:.2f}\t{pos_now[i+1]:.2f}\t{pos_now[i+2]:.2f}\t{pos_now[i+3]:.2f}"
            )

        # We call the advanced function internally.
        # Note the velocities here are in ticks, not deg/s or rad/s, so we don't scale them.
        self.check_connected()
        assert len(motor_ids) == len(positions)
        for i, motor_id in enumerate(motor_ids):
            pos_ticks = int(positions[i] / self.pos_scale)
            # --- CRITICAL SAFETY CHECK ---
            if not (0 <= pos_ticks <= 4096):
                logging.critical(
                    f"FATAL: Position command for motor ID {motor_id} is {pos_ticks}, which is out of the valid range (0-4096)."
                )
                logging.critical(
                    "Disabling torque on all motors for safety and quitting."
                )
                self.set_torque_enabled(self.motor_ids, False)
                raise ValueError(
                    f"Position command for motor {motor_id} is out of valid range."
                )
            print(f"[ID:{motor_id:03d}]: {pos_ticks} ticks, rad={pos_ticks * self.pos_scale:.2f}")
            addparam_result = self.HLSSyncWritePosEx(motor_id, pos_ticks, 1000, 0)
            if not addparam_result:
                logging.error(f"[ID:{motor_id:03d}] SyncWritePosEx add param failed")

        comm_result = self.packet_handler.groupSyncWrite.txPacket()
        self.handle_packet_result(comm_result, context="groupSyncWrite.txPacket")
        self.packet_handler.groupSyncWrite.clearParam()

    def write_desired_pos_vel_acc(
        self,
        motor_ids: Sequence[int],
        positions: np.ndarray,
        velocities: np.ndarray,
        accels: np.ndarray,
    ):
        """
        Writes desired positions, velocities, and accelerations to motors.
        Includes a critical safety check for position range.
        Units (deg or rad) are determined by the `use_degrees` flag set at initialization.
        """
        self.check_connected()
        assert len(motor_ids) == len(positions) == len(velocities) == len(accels)

        for i, motor_id in enumerate(motor_ids):
            pos_ticks = int(positions[i] / self.pos_scale)
            vel_ticks = int(abs(velocities[i] / self.vel_scale))
            acc_val = int(accels[i])

            # --- CRITICAL SAFETY CHECK ---
            if not (0 <= pos_ticks <= 4096):
                logging.critical(
                    f"FATAL: Position command for motor ID {motor_id} is {pos_ticks}, which is out of the valid range (0-4096)."
                )
                logging.critical(
                    "Disabling torque on all motors for safety and quitting."
                )
                self.set_torque_enabled(self.motor_ids, False)
                raise ValueError(
                    f"Position command for motor {motor_id} is out of valid range."
                )

            addparam_result = self.HLSSyncWritePosEx(
                motor_id, pos_ticks, vel_ticks, acc_val
            )
            if not addparam_result:
                logging.error(f"[ID:{motor_id:03d}] SyncWritePosEx add param failed")

        comm_result = self.packet_handler.groupSyncWrite.txPacket()
        self.handle_packet_result(comm_result, context="groupSyncWrite.txPacket")
        self.packet_handler.groupSyncWrite.clearParam()

    def check_connected(self):
        """Raises an exception if the client is not connected."""
        if not self.is_connected:
            raise RuntimeError("Client is not connected. Call connect() first.")

    def handle_packet_result(
        self,
        comm_result: int,
        ft_error: Optional[int] = 0,
        ft_id: Optional[int] = None,
        context: Optional[str] = None,
    ):
        """Handles the result from a communication request, logging any errors."""
        if comm_result != COMM_SUCCESS:
            message = (
                f"{context or ''}: {self.packet_handler.getTxRxResult(comm_result)}"
            )
            if ft_id is not None:
                message = f"[ID:{ft_id:03d}] {message}"
            logging.error(message)
            return False
        elif ft_error != 0:
            message = (
                f"{context or ''}: {self.packet_handler.getRxPacketError(ft_error)}"
            )
            if ft_id is not None:
                message = f"[ID:{ft_id:03d}] {message}"
            logging.error(message)
            return False
        return True

    def __enter__(self):
        self.connect()
        return self

    def __exit__(self, *args):
        self.disconnect()


@atexit.register
def ft_cleanup_handler():
    """Ensures all motor clients are properly disconnected on exit."""
    open_clients = list(FTClient.OPEN_CLIENTS)
    for client in open_clients:
        logging.warning("Client was not disconnected. Forcing disconnect.")
        # Ensure torque is off on cleanup, just in case.
        try:
            if client.is_connected:
                client.set_torque_enabled(client.motor_ids, False)
        except Exception as e:
            logging.error(f"Error during final cleanup torque disable: {e}")
        client.disconnect()


class FTReader:
    """
    Generic base class for reading data from FT motors using GroupSyncRead.
    """

    def __init__(self, client, motor_ids: Sequence[int], address: int, size: int):
        self.client = client
        self.motor_ids = motor_ids
        self.address = address
        self.size = size
        self.operation = GroupSyncRead(client.packet_handler, address, size)
        for motor_id in self.motor_ids:
            success = self.operation.addParam(motor_id)
            if not success:
                raise OSError(
                    f"[ID:{motor_id:03d}] Could not add motor to GroupSyncRead operation."
                )
        self._initialize_data()

    def read(self):
        """Reads data from the motors."""
        self.client.check_connected()
        comm_result = self.operation.txRxPacket()
        if not self.client.handle_packet_result(comm_result, context="GroupSyncRead"):
            return self._get_data()

        errored_ids = []
        for i, motor_id in enumerate(self.motor_ids):
            is_available, scs_error = self.operation.isAvailable(
                motor_id, self.address, self.size
            )
            if (
                self.client.handle_packet_result(
                    0, scs_error, motor_id, "GroupSyncRead.isAvailable"
                )
                and is_available
            ):
                self._update_data(i, motor_id)
            else:
                errored_ids.append(motor_id)

        if errored_ids:
            logging.warning(
                "GroupSyncRead data unavailable for IDs: %s", str(errored_ids)
            )
        pos_now = self._get_data()-3.14
        print("Read Position:")
        for i in range(0, len(pos_now), 4):
            print(f"{pos_now[i]:.2f}\t{pos_now[i+1]:.2f}\t{pos_now[i+2]:.2f}\t{pos_now[i+3]:.2f}")
        return self._get_data()

    def _initialize_data(self):
        raise NotImplementedError

    def _update_data(self, index: int, motor_id: int):
        raise NotImplementedError

    def _get_data(self):
        raise NotImplementedError


class FTPosVelReader(FTReader):
    """Reads both Position and Velocity in a single GroupSyncRead operation."""

    def __init__(self, client, motor_ids: Sequence[int]):
        super().__init__(client, motor_ids, SMS_STS_PRESENT_POSITION_L, 4)

    def _initialize_data(self):
        self._pos_data = np.zeros(len(self.motor_ids), dtype=np.float32)
        self._vel_data = np.zeros(len(self.motor_ids), dtype=np.float32)

    def _update_data(self, index: int, motor_id: int):
        pos_raw = self.operation.getData(
            motor_id, SMS_STS_PRESENT_POSITION_L, LEN_PRESENT_POSITION
        )
        vel_raw = self.operation.getData(
            motor_id, SMS_STS_PRESENT_SPEED_L, LEN_PRESENT_SPEED
        )
        self._pos_data[index] = (
            unsigned_to_signed(pos_raw, size=2) * self.client.pos_scale
        )
        self._vel_data[index] = (
            unsigned_to_signed(vel_raw, size=2) * self.client.vel_scale
        )

    def _get_data(self):
        return self._pos_data.copy(), self._vel_data.copy()


class FTPosReader(FTReader):
    """Reads only Position using a GroupSyncRead operation."""

    def __init__(self, client, motor_ids: Sequence[int]):
        super().__init__(
            client, motor_ids, SMS_STS_PRESENT_POSITION_L, LEN_PRESENT_POSITION
        )

    def _initialize_data(self):
        self._pos_data = np.zeros(len(self.motor_ids), dtype=np.float32)

    def _update_data(self, index: int, motor_id: int):
        pos_raw = self.operation.getData(
            motor_id, SMS_STS_PRESENT_POSITION_L, LEN_PRESENT_POSITION
        )
        # self._pos_data[index] = pos_raw
        self._pos_data[index] = (
            unsigned_to_signed(pos_raw, size=2) * self.client.pos_scale
        )

    def _get_data(self):
        return self._pos_data.copy()


class FTVelReader(FTReader):
    """Reads only Velocity using a GroupSyncRead operation."""

    def __init__(self, client, motor_ids: Sequence[int]):
        super().__init__(client, motor_ids, SMS_STS_PRESENT_SPEED_L, LEN_PRESENT_SPEED)

    def _initialize_data(self):
        self._vel_data = np.zeros(len(self.motor_ids), dtype=np.float32)

    def _update_data(self, index: int, motor_id: int):
        vel_raw = self.operation.getData(
            motor_id, SMS_STS_PRESENT_SPEED_L, LEN_PRESENT_SPEED
        )
        self._vel_data[index] = (
            unsigned_to_signed(vel_raw, size=2) * self.client.vel_scale
        )

    def _get_data(self):
        return self._vel_data.copy()
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

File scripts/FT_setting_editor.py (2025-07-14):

#!/usr/bin/env python
#
# ********* Feetech Motor Utility Script *********
#
# This script provides an interactive command-line interface to configure
# Feetech HTS/STS series smart servos.
#
# Features:
# 1. (Mode 0) Center Calibration: Interactively sets the center position (offset)
#    for motors one by one.
#
# 2. (Mode 1) Batch PID Editor: Sets the P, I, and D position gains for all
#    connected servos at once.
#
# 3. (Mode 2) Batch Generic Write: A powerful tool to write any value to a
#    specific register address on all or a selected subset of connected motors.
#
# 4. (Mode 3) Batch Generic Read: Reads and displays data from a specific
#    register address for all or a selected subset of connected motors.
#

from scservo_sdk import *
import sys
import os
import time
import threading

# Add the path to the scservo_sdk library
# The '..' assumes the script is in an 'examples' folder next to 'scservo_sdk'
# Adjust this path if your folder structure is different.
sys.path.append("..")

# --- Configuration ---
# Your serial port name.
# Windows: "COM1", "COM2", etc.
# Linux: "/dev/ttyUSB0", "/dev/ttyAMA0", etc.
# Mac: "/dev/tty.usbserial-*"
PORT_NAME = '/dev/ttyUSB0'

# Baudrate for the motors
BAUDRATE = 115200

# Motor ID scan range
MIN_ID = 0
MAX_ID = 50

# --- Control Table Addresses ---
SMS_STS_TORQUE_ENABLE = 40
SMS_STS_PRESENT_POSITION_L = 56
INST_RECENTER = 11

# --- PID EEPROM Registers (Position Loop) ---
SMS_STS_POS_P = 21 # Kp: Position Loop P Gain
SMS_STS_POS_D = 22 # Kd: Position Loop D Gain
SMS_STS_POS_I = 23 # Ki: Position Loop I Gain

# The desired center position value. The calibration command sets it to 2048.
TARGET_CENTER_POSITION = 2048

# --- Global variable for the position reading thread ---
stop_thread = threading.Event()


def position_reader_thread(packetHandler, motor_id):
    """A thread that continuously reads and displays the motor's position."""
    print("\nStarting real-time position display...")
    while not stop_thread.is_set():
        scs_present_position, _, scs_comm_result, scs_error = packetHandler.ReadPosSpeed(motor_id)
        if scs_comm_result == COMM_SUCCESS and scs_error == 0:
            sys.stdout.write(
                f"\rCurrent Position: {scs_present_position:04d} | Move motor to desired center, then press Enter to confirm.")
            sys.stdout.flush()
        else:
            sys.stdout.write(
                f"\rError reading position. Check connection. Comm: {packetHandler.getTxRxResult(scs_comm_result)}, Err: {packetHandler.getRxPacketError(scs_error)}")
            sys.stdout.flush()
            if scs_comm_result != COMM_SUCCESS:
                break
        time.sleep(0.1)


def ping_for_motors(packetHandler):
    """Scans for available motors and returns a list of their IDs."""
    print("Pinging for motors...")
    available_ids = []
    for motor_id in range(MIN_ID, MAX_ID + 1):
        _, scs_comm_result, scs_error = packetHandler.ping(motor_id)
        if scs_comm_result == COMM_SUCCESS and scs_error == 0:
            sys.stdout.write(f"\rFound motor with ID: {motor_id}   ")
            sys.stdout.flush()
            available_ids.append(motor_id)
            time.sleep(0.01)
    print("\n")
    return available_ids


def select_motor_from_list(available_ids):
    """Prompts the user to select a motor from a list of IDs."""
    print(f"Available motor IDs: {available_ids}")
    while True:
        try:
            choice = input("Enter the ID of the motor to calibrate (or type 'q' to quit): ")
            if choice.lower() == 'q':
                return None
            chosen_id = int(choice)
            if chosen_id in available_ids:
                return chosen_id
            else:
                print("Invalid ID. Please choose from the available list.")
        except ValueError:
            print("Invalid input. Please enter a number.")


def recenter_motor_command(packetHandler, scs_id):
    """Sends the raw, low-level recenter command (Instruction 11)."""
    txpacket = [0] * 6
    txpacket[2] = scs_id
    txpacket[3] = 2
    txpacket[4] = INST_RECENTER
    _, result, error = packetHandler.txRxPacket(txpacket)
    return result, error


def calibrate_motor(packetHandler, motor_id):
    """Guides the user through the calibration process for a single motor."""
    print(f"\n--- Calibrating Motor ID: {motor_id} ---")
    global stop_thread
    stop_thread.clear()
    reader = threading.Thread(target=position_reader_thread, args=(packetHandler, motor_id))
    reader.start()
    input()
    stop_thread.set()
    reader.join()
    print("\n")

    print("Writing calibration command to motor EEPROM...")
    scs_comm_result, _ = packetHandler.write1ByteTxRx(motor_id, SMS_STS_TORQUE_ENABLE, 0)
    if scs_comm_result != COMM_SUCCESS:
        print("Error: Failed to disable torque.")
        return
    print("Torque disabled.")
    time.sleep(0.05)

    scs_comm_result, _ = packetHandler.unLockEprom(motor_id)
    if scs_comm_result != COMM_SUCCESS:
        print("Error: Failed to unlock EEPROM.")
        return
    print("EEPROM unlocked.")
    time.sleep(0.05)

    scs_comm_result, _ = recenter_motor_command(packetHandler, motor_id)
    if scs_comm_result != COMM_SUCCESS:
        print("Error: Failed to send recenter command.")
        packetHandler.LockEprom(motor_id)
        return
    print("Recenter command sent successfully.")
    time.sleep(0.05)

    scs_comm_result, _ = packetHandler.LockEprom(motor_id)
    if scs_comm_result != COMM_SUCCESS:
        print("CRITICAL ERROR: Failed to re-lock EEPROM. The change may not be saved.")
    else:
        print("EEPROM re-locked. Change is saved.")
    time.sleep(0.05)

    print(f"\n--- Calibration Complete for Motor ID: {motor_id} ---")


def get_pid_input():
    """Gets and validates PID values from the user."""
    while True:
        try:
            p_val = int(input("Enter P gain (0-254): "))
            d_val = int(input("Enter D gain (0-254): "))
            i_val = int(input("Enter I gain (0-254): "))
            if 0 <= p_val <= 254 and 0 <= d_val <= 254 and 0 <= i_val <= 254:
                return p_val, d_val, i_val
            else:
                print("Error: All values must be between 0 and 254.")
        except ValueError:
            print("Invalid input. Please enter numbers only.")
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

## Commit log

2025-06-29 init commit
    [H101.STL, S101.STL, S101_Slim.STL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]
2025-07-07 The hand mount `hand_mount.3mf`. You can mount the LEAP Hand with the hand mount using 4 M6 screws.
    [hand_mount.3mf]
2025-07-07 added sldprts for modified STLs
    [H101.SLDPRT, S101.sldprt, S101_Slim.sldprt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]
2025-07-14 Added FT_setting.py and some STLs so people dont have to convvert them in SolidWorks anymore. Yay
    [BWYI-C-d8-L10.step, FT-Hand3-Thumb.SLDASM, FT-Hand3.SLDASM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]
2025-07-14 add FT_links
    [fingertip_custom_real.STL, statistical List.xlsx, 硅胶模具_内.STL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]
2025-07-16 Update hand_mount.3mf
    update corrupted 3mf file
    [hand_mount.3mf]
